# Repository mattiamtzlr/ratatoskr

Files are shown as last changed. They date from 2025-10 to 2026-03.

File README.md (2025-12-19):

# CS-358a Project: Ratatoskr (Micromouse)

Team members: Leoluca Bernardi, Leonardo Bolognese, Ali Gorgani, Mattia Metzler, Anthony Tamberg



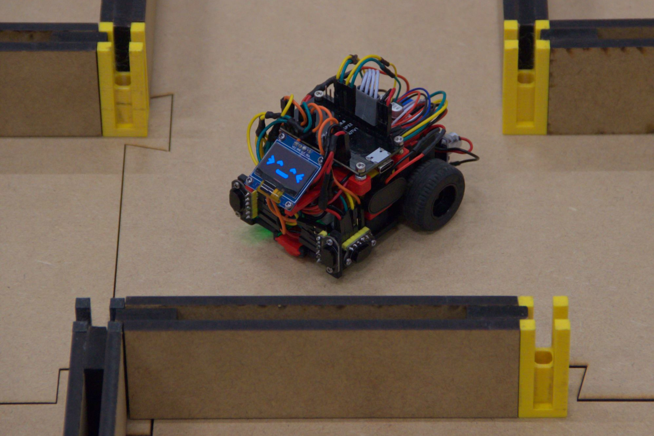
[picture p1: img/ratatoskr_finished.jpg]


## Table of Contents

<!-- mtoc-start -->

* [Introduction](#introduction)
  * [Inspiration and References](#inspiration-and-references)
* [Design](#design)
  * [Hardware](#hardware)
    * [Schematic](#schematic)
  * [Firmware and Software](#firmware-and-software)
    * [Firmware](#firmware)
    * [Software and Logic](#software-and-logic)
  * [The Maze](#the-maze)
* [Assembly](#assembly)
  * [3D-printing](#3d-printing)
  * [Soldering](#soldering)
  * [Chassis](#chassis)
  * [Drivetrain and Housing](#drivetrain-and-housing)
  * [Battery and ESP32 Mount](#battery-and-esp32-mount)
  * [OLED Mount](#oled-mount)
  * [Wiring, Motor driver and Power Supply](#wiring-motor-driver-and-power-supply)
    * [Communication Cable Trees](#communication-cable-trees)
    * [Battery Connector, Buck Converter and Motor Driver](#battery-connector-buck-converter-and-motor-driver)
    * [ESP32](#esp32)
    * [XSHUT Cables](#xshut-cables)
* [Software Setup](#software-setup)
  * [PIO Setup](#pio-setup)
  * [MMS Setup](#mms-setup)

<!-- mtoc-end -->

<br>

## Introduction

Ratatoskr is a small autonomous robotic 'micromouse' that can find the fastest path through a maze.
In two separate `search` and `run` phases, the mouse first finds the most optimal path and then traverses it, doing
both in the shortest possible time. In this project we designed a compact micromouse capable of traversing a maze
smoothly, precisely, and efficiently, allowing it to take diagonal paths during the final `run`.  
Below is a video showing both these phases. The start is marked in blue and the goal in red. The `run`
phase starts once the mouse has returned back to the start.

https://github.com/user-attachments/assets/a93646fe-425e-46f5-a616-213aecb9d267

### Inspiration and References

This project is inspired by the micromice of a previous iteration of the course, specifically
[MinosMouse](https://github.com/epfl-cs358/2024fa-minosmouse) and
[PicoMouse](https://github.com/epfl-cs358/2024fa-picomouse). We used their projects to get an idea of the needed
components and the general layout of the software.  
We also used parts of their maze for convenience and to save on resources and waste, because remaking these would
use a lot of material and time. There is more about this in the maze section.

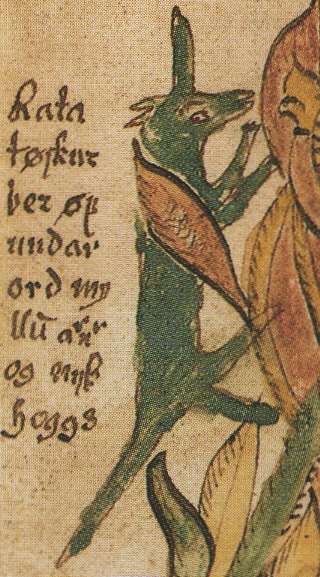
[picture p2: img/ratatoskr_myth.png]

Finally, the name 'Ratatoskr' comes from Norse mythology and refers to a squirrel that runs through the world-tree
Yggdrasil, carrying messages. We found this name to be quite fitting for our project, as Ratatoskr is one of the only
creatures capable of navigating the complex interior of Yggdrasil.
For your enjoyment, here is an image from a 17<sup>th</sup> icelandic manuscript depicting Ratatoskr, taken from Wikipedia
(public domain).

<br>

## Design

By design, most parts of Ratatoskr are fully 3D-printable, with the remaining parts being common Lego pieces.  
The final Micromouse weighs approximately 190g, it is 7cm wide and about 10cm long. About a quarter of the weight comes
from the 9V battery used to power it.

### Hardware

Ratatoskr requires the following electronic and mechanical components:
| Component | Quantity | Notes |
|---|---|---|
| N20 DC gear motor w/ encoder and connector | 2 | Working RPMs: 500, 750, 300[^1] |
| MX1508 motor driver | 1 | - |
| ESP32 development kit | 1 | **30-pin** version, higher should be fine |
| LM2596 buck converter | 1 | - |
| VL53L1X time-of-flight sensor | 4 | Also known as `TOF400C` |
| MPU-6050 3-axis accelerometer w/ gyroscope | 1 | - |
| SSD1306 OLED screen | 1 | These come in multiple colors, we used hybrid yellow-blue |
| 9V (PP3) battery w/ connector | 1 | We recommend using good quality batteries for this, as the current should be somewhat stable |
| LEGO(r) 58090 Tire 30.4 x 14 Solid | 2 | Other tires of approximately the same size should work |
| LEGO(r) 3705 Technic Axle 4L | 2 | - |

[^1]: Not tested, but should work given the torque and speed requirements

#### Schematic

Below is the full electronics schematic of ratatoskr.

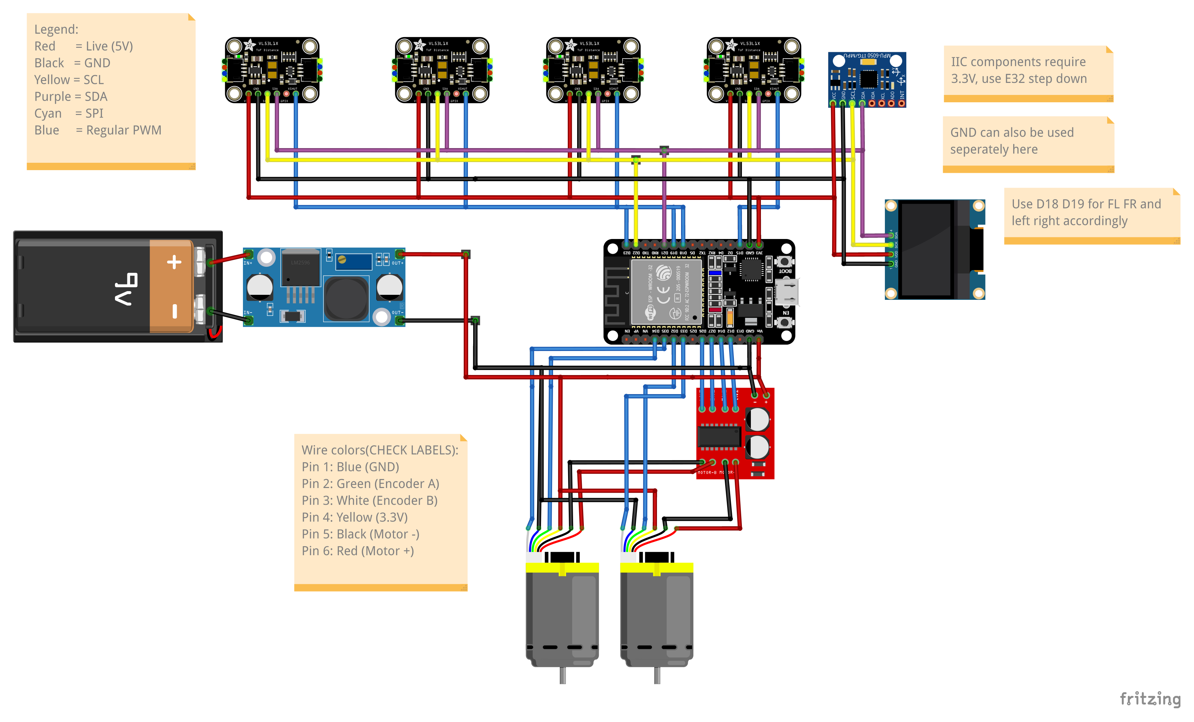
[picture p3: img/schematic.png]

Note that the exact pinout of the components might differ depending on the manufacturer and version of each part.

### Firmware and Software

Below follows a very brief overview of how the software for Ratatoskr works. For more details look at the source code :wink:

#### Firmware

We use the following libraries to simplify the hardware interfaces:

| Library | Used for |
| --- | --- |
| [pololu/VL53L1X](https://github.com/pololu/vl53l1x-arduino) | ToF sensors |
| [ronny-antoon/NVSDatabase](https://github.com/ronny-antoon/DatabaseAPI) | Flash storage database |
| [adafruit/Adafruit_SSD1306](https://github.com/adafruit/Adafruit_SSD1306) | OLED screen |
| [robjen/GFX_fonts](https://github.com/robjen/GFX_fonts) | Font for the OLED screen |

Additionally, we use [PlatformIO](https://platformio.org/) to compile the source code for the ESP32 and to handle all
the libraries above. See [PIO Setup](#pio-setup) for more details.

All sensors communicate with the ESP over the I<sup>2</sup>C protocol because the components can be assigned to
different addresses. As a result, we can use the same SDA and SCL pins for them. ToF sensors additionally require an extra pin for some XSHUT logic. The OLED is also controlled via I<sup>2</sup>C.  
There are C++ classes for most components that handle all their low-level functionality and provide a clean, high-level
interface for interacting with them.

#### Software and Logic

To make testing easier we use [MMS](https://github.com/mackorone/mms), a micromouse simulator. It allows us to test the
higher level code that handles solving a maze and calculating the final run without physically needing to run Ratatoskr
in a maze.

<p align="center"><video src='https://github.com/user-attachments/assets/aed72121-12ea-4d18-b9f5-ffeec3736798' height=100 width=100/></video></p>

Ratatoskr uses _principal-integral-derivative_ (PID) controllers to generate precise and stable movement. These
controllers continually adjust the motor power based on sensor feedback, allowing the micromouse to correct itself on the
fly. There are three PID systems in total:

1. Motor encoders: ensure that both wheels spin at the same, correct rate allowing for controlled acceleration.
2. Side ToF sensors: ensure the mouse stays centered between the walls and generally positions itself correctly in the
   maze.
3. Front ToF sensors: ensure that the mouse stays centered during diagonals and detect the end of diagonals.

To find the best path in the maze, Ratatoskr uses a floodfill algorithm while regularly updating its image of the maze
using the sensors. The best path is then computed from a Dijkstra graph constructed from this information. The Dijkstra
algorithm is tuned to favor diagonals over turns. This path is finally further optimized to combine multiple forward
movements into one so that Ratatoskr does not stop at every cell.

Documentation can be accessed by running `make docs` at project root. By using [Doxygen](https://www.doxygen.nl/index.html)
and a [CSS extension](https://github.com/jothepro/doxygen-awesome-css/tree/1f3620084ff75734ed192101acf40e9dff01d848) all
function headers get collected into a nice multipage format including function headers, descriptions, and call-graphs.

### The Maze

The maze we use for Ratatoskr uses the same wall pieces and mounting posts designed by the previous year's micromice teams, although with a newly
designed tiled floor. The posts are 3D-printed with a pocket for an M2.5 nut. The walls and baseplates are lasercut
from MDF.  
As a sidenote, it probably would have been better to redesign the posts and walls because they are not easy
to assemble and use. However, to save resources and time, we decided to go with the existing ones.  
To mount the posts to the baseplates, use M2.5 flathead screws, which can be countersunk to the underside of
the baseplates with a tapered (hand) drill. The walls are simply slid in between the posts.

The baseplates are designed to interlock like puzzle tiles, eliminating the need for complex mounting

Below is a technical drawing of a maze baseplate.

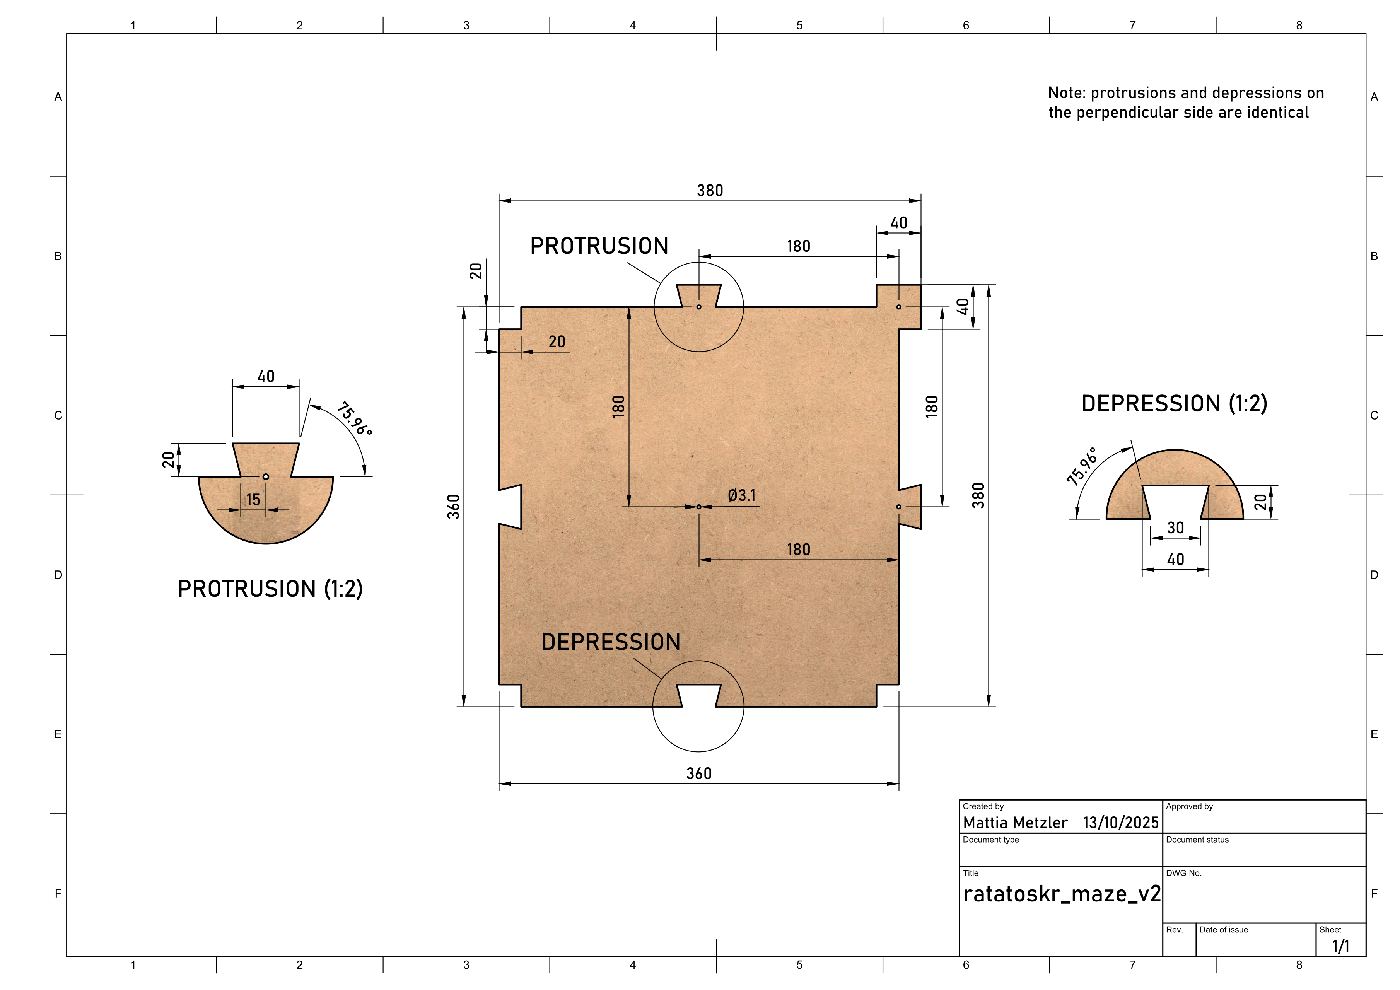
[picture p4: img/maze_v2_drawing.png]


<br>

## Assembly

To assemble Ratatoskr, the following additional hardware is needed:

| Item | Quantity | Note |
| --- | --- | --- |
| M2.5 threaded inserts | 6 | 4x for ESP32 mount, 2x for chassis |
| 2.5mm washers | 6 | Used to increase mount height of gyro |
| 5mm washers | 2 | Used to reduce friction between wheel and chassis |
| M2.5 nuts | 6 | 2x for gyro, 4x for ESP32 mount |
| M2.5 10mm machine screws | 8 | 2x for battery holder, 2x for gyro, 4x for ESP32 mount |
| M2.5 5mm machine screws  | 3 | 2x for buck converter, 1x for motor driver |
| M2 5mm machine screws | 12 | 2x for each ToF sensor, 4x for OLED |

In addition:

- Various jumper cables, depending on the amount of serviceability desired.
- There is an alternative version of the ball caster piece (see below) which has a screw hole for a M2.5 5mm machine
screw to reduce wear on the plastic. We found however that that version leads to more snagging on the maze tile borders.

### 3D-printing

The following STL files need to be 3D-printed:

| STL file | Quantity | Description and Notes |
| --- | --- | --- |
| `./CAD/STL/miter_gear.stl` | 4 | Drivetrain gears |
| `./CAD/STL/lego_adapter_v2b.stl`  | 2 | Motor shaft adapters, **brim recommended** |
| `./CAD/STL/screen_mount.stl` | 2 | OLED screen mounts, **brim needed** |
| `./CAD/STL/v2/ball_caster.stl` | 1 | Ball caster, **Supports recommended** |
| `./CAD/STL/v2/battery_clip.stl` | 1 | Battery clip |
| `./CAD/STL/v2/battery_holder.stl` | 1 | Battery holder, **Supports needed** |
| `./CAD/STL/v2/chassis_cutout.stl` | 1 | Latest, Lightest ver. of chassis, **supports needed for axle holes and sidewall cutouts** |
| `./CAD/STL/v2/middle_shelf.stl` | 1 | Shelf to mount gyro on |
| `./CAD/STL/v2/top_shelf.stl` | 1 | Shelf to mount motor driver on |

It is recommended to print all parts on Prusa MK4 printers, splitting the job into two prints: the chassis and the
remaining components.  
After that is done, heat-set the threaded inserts into the battery holder and the chassis:

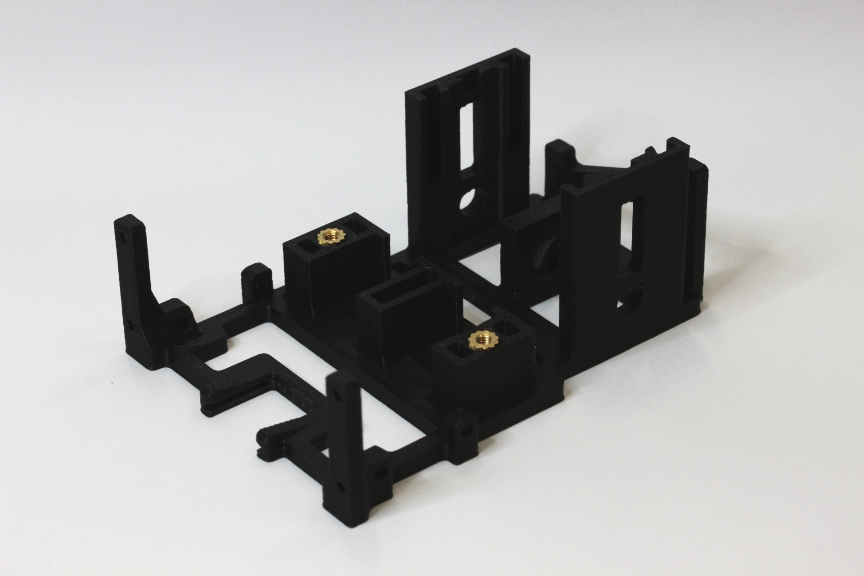
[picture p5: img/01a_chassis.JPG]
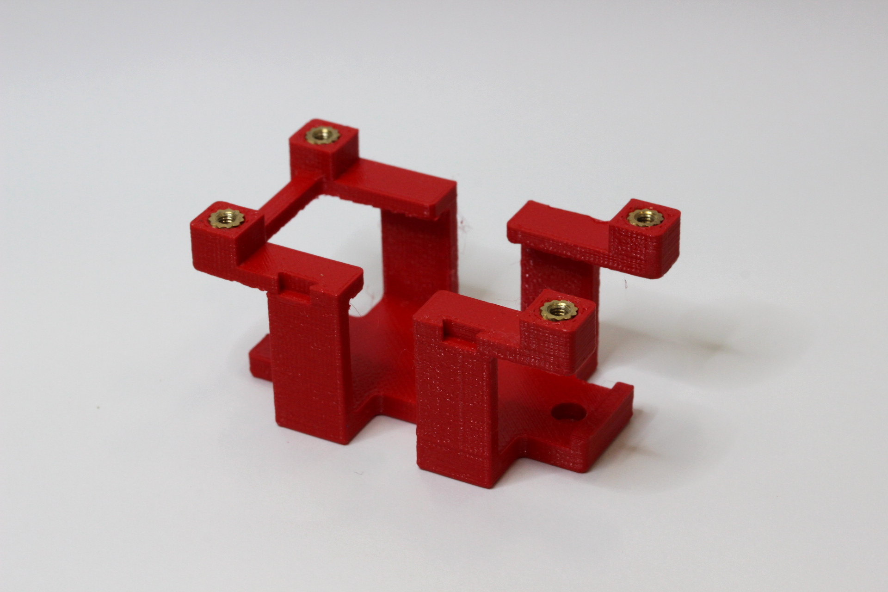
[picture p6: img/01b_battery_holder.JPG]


### Soldering

Solder the pin headers to the OLED, the ToF sensors and the gyroscope. Use the bent headers for the ToF and the gyro,
inserting them from below for the ToFs and from above for the gyro. Bending the OLED headers inwards slightly helps.  
For more details see photos further below.

### Chassis

Insert the inverted (!) ball-caster into the cutout in the front. You shouldn't need to sand this much once the supports
are removed, as it has been designed with the right tolerances.  
Mount the ToF sensors as shown below to the chassis using 2x M2 5mm screws each.

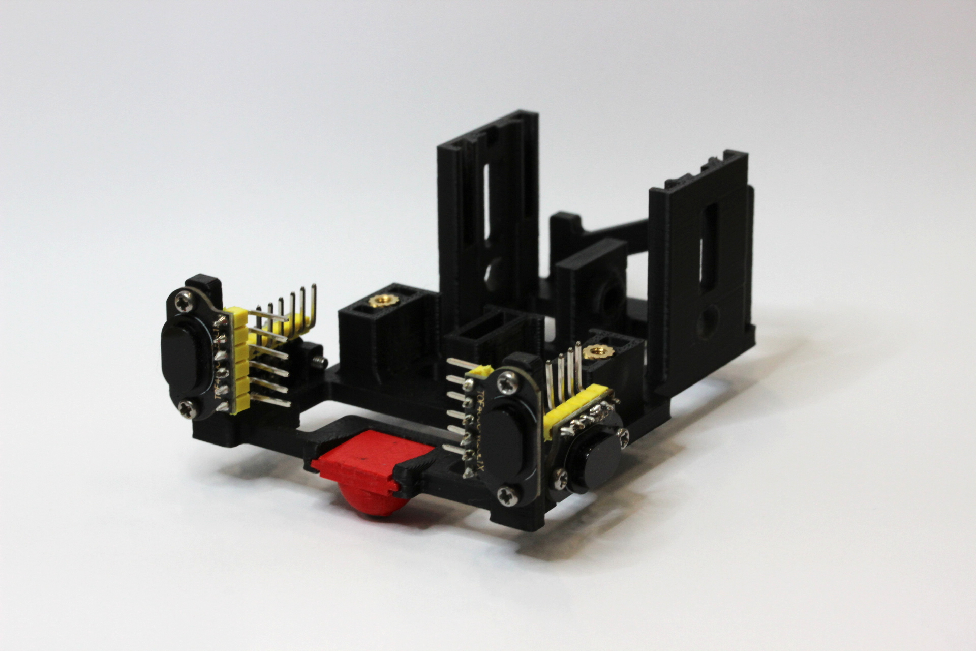
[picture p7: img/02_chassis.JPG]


### Drivetrain and Housing

Screw the gyro to the middle shelf of the drivetrain housing making sure to put three (3) washers between the underside
of the gyro and the shelf, and a nut at the underside of the shelf. Use 2x M2.5 10mm screws. Take note of the
orientation of the gyro in the picture below -- the back edge of the gyro should be aligned with the edge of the shelf.  
Then slide the shelf down the rails in the drivetrain housing. Again, you will probably need to sand/file some things here.

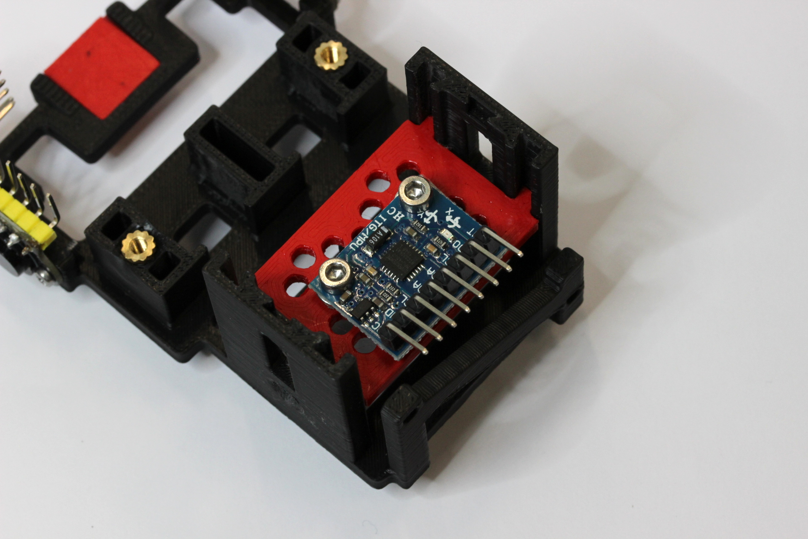
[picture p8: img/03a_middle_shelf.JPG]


Put one adapter over each motor shaft and slide on a gear. Insert the LEGO axles into the assembled wheels, put the
washer on top and slide them through the axle holes in the chassis, while simultaneously putting in the second set of
gears. This step is somewhat tricky but well doable with some pliers or tweezers.  
Before doing this, you need to file down the insides of the axle holes (including the holder in the middle) to make sure
the wheels turn freely. This is again somewhat finnicky but well doable with a small round file.

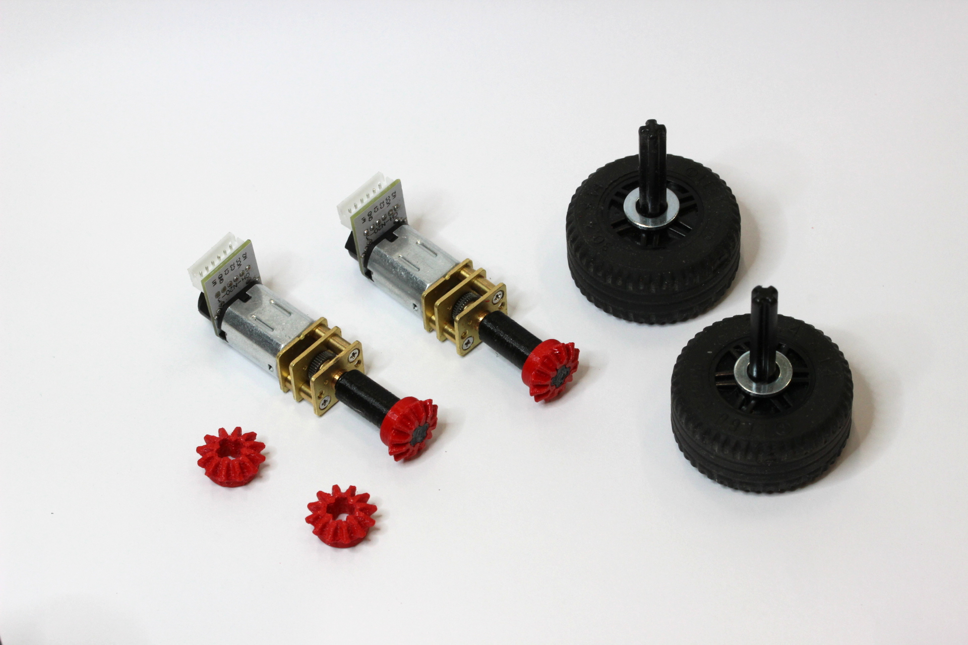
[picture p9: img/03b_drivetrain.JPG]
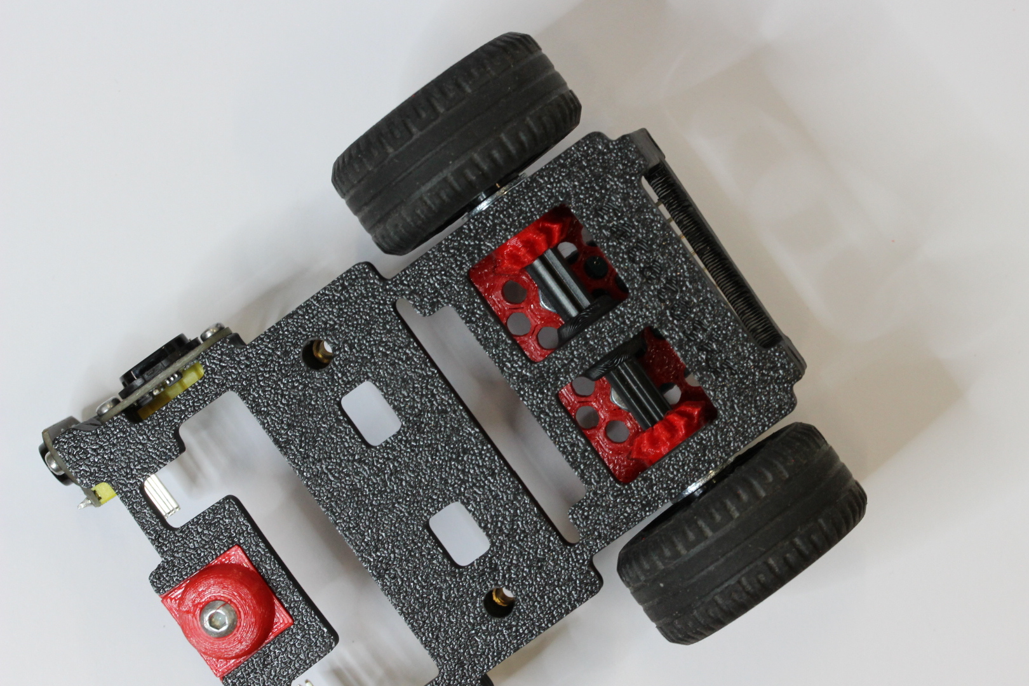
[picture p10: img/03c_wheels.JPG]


Finally, insert the motors as shown below. You might need to turn the wheels a bit so the gears mesh well.

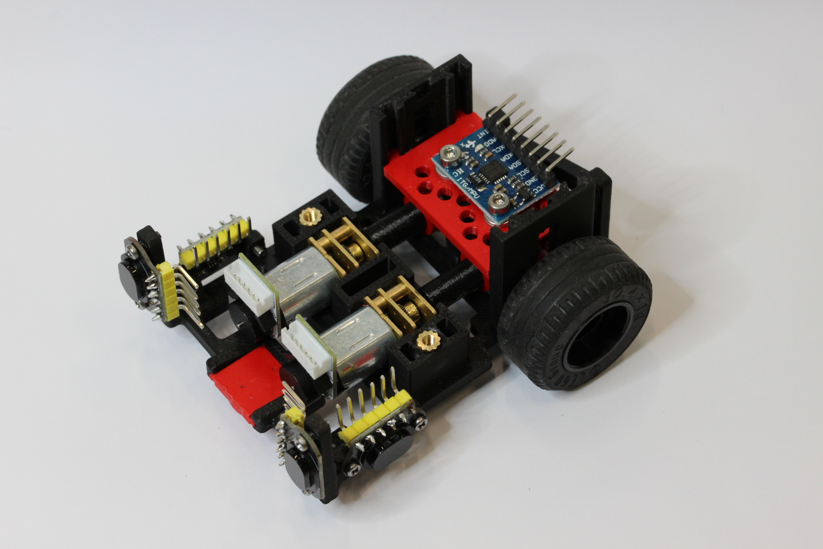
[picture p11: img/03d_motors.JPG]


### Battery and ESP32 Mount

Use 2x M2.5 10mm screws to screw the battery holder to the chassis using the previously installed threaded inserts. Make
sure to orient the battery holder correctly, the cutouts for the OLED mounts should be facing forwards. Alternatively,
check that the little connecting bar on one side of the battery holder faces the right-hand side.  
Also make sure that the screws are inserted all the way, i.e. the heads should sink into the cutouts made for them.

At this point you can slide in the battery and secure it from behind using the little clip.

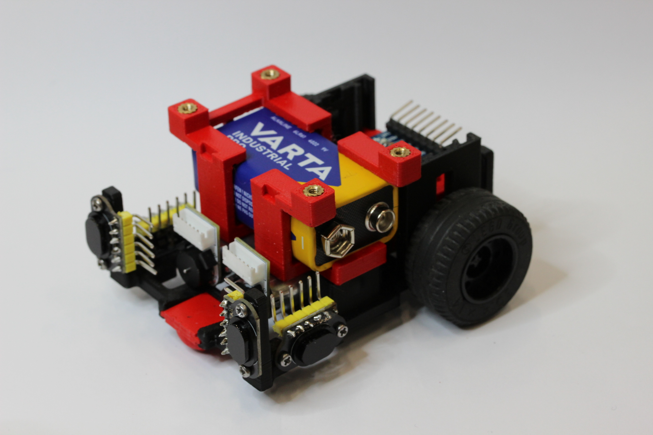
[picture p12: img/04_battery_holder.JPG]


### OLED Mount

Using 4x M2 5mm screws, screw the OLED mounts to the OLED board like in the below photo:

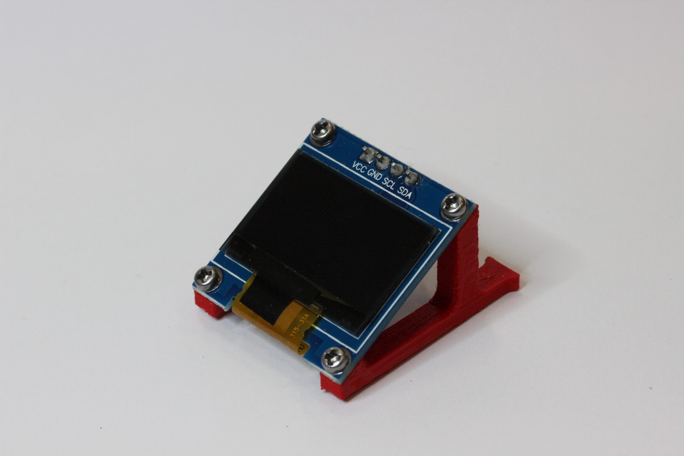
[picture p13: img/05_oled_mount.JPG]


### Wiring, Motor driver and Power Supply

Now for the hard part! :wink:

#### Communication Cable Trees

You need to wire **four** (4) cable trees with female dupont connectors for the
I<sup>2</sup>C communication as follows:

- four (4) connectors for the ToF sensors
- one (1) connector each for the gyro and the OLED

Therefore you need (6) female connectors in total, first split into two, one for ToFs/OLED and one for gyro, the former
then further split into five.  
We recommend keeping the colors between the trees different so they are easier to tell apart, as in the photos below.

> [!WARNING]
> It is crucial to make these cables the right length. Too short and you won't be able to connect the components, too long
> and there will not be enough space in the mouse to put all the cables. Measure the cables before you cut them by
> dry-fitting them on the mouse.

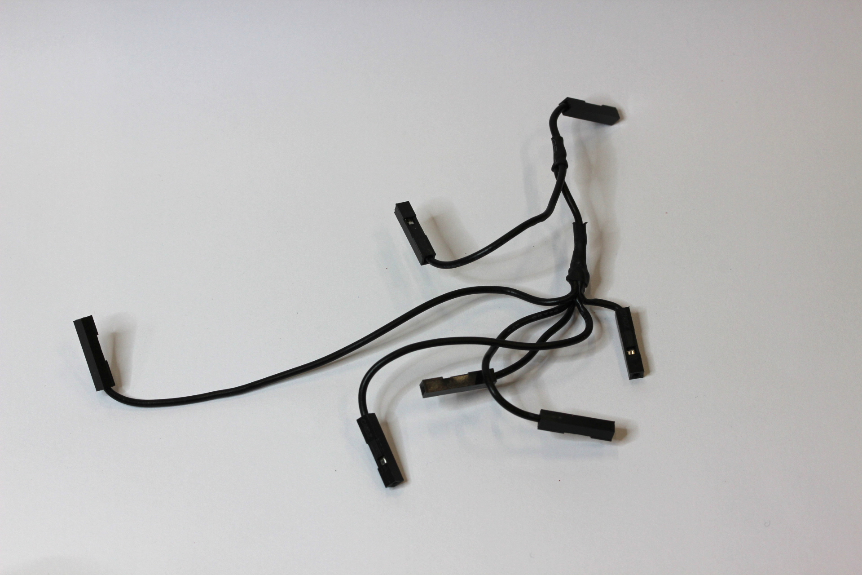
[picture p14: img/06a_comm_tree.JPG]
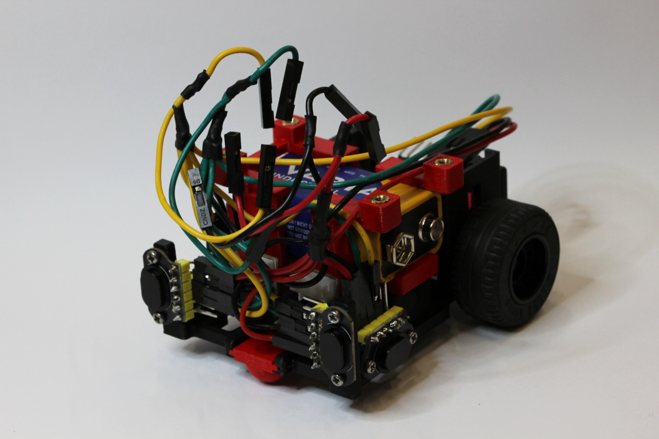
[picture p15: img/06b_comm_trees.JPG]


The four down-facing unused connectors in the above picture are used for the OLED screen, which can also be mounted now
by sliding it into the cutouts on the battery holder.

#### Battery Connector, Buck Converter and Motor Driver

The buck converters `IN +` and `IN -` pads need to be soldered to the power (red) and ground (black) cables of the
battery connector respectively. Then, with a multimeter connected to the `OUT +` and `OUT -` pads, the brass screw on
the buck converter needs to be turned (probably counter-clockwise) until the voltage read is around 5V. The LED on the
buck converter should light up quite strongly when the battery is connected.

Then wire up **two** (2) cable trees for 5V and GND going from one cable to four each. As the power wires need to be
reliable, these should be soldered directly, not using Dupont connectors. Thus only add Dupont connectors to one of the
four cables, namely the one for the ESP32.  
Then wire the other three cables to the motor drivers and the motors directly. Finish soldering the motor driver as shown
on the [schematic](#schematic).  
The encoder and motor input cables should also end in Dupont connectors to connect to the ESP32.

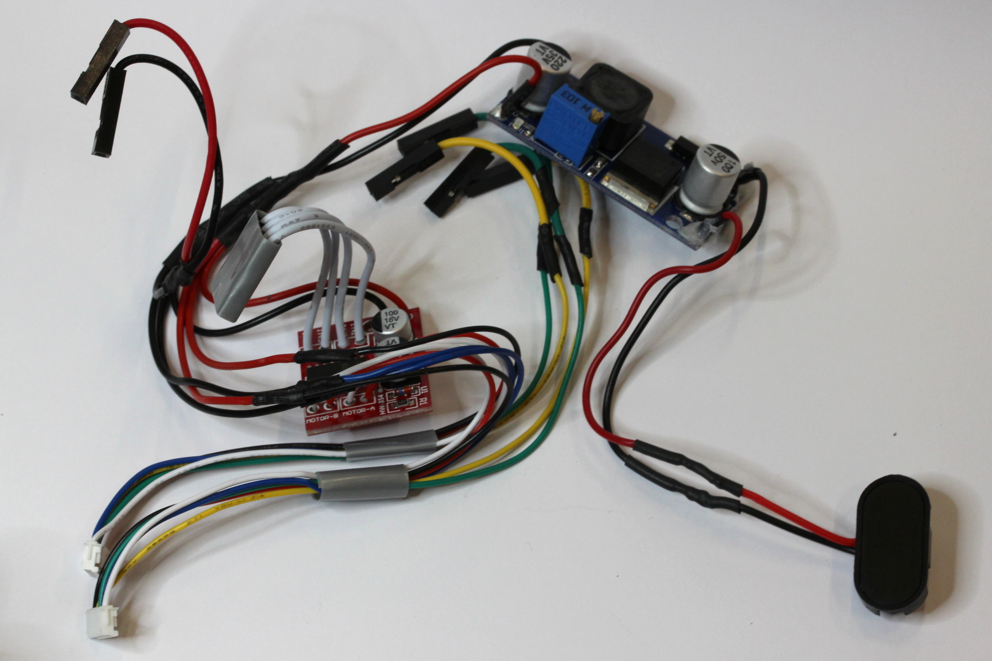
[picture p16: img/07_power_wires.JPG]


Finally, mount all of this to the mouse, making sure that the motors are plugged in correctly. To do so, first mount
the motor driver to the top shelf using 1x M2.5 5mm screw. The buck converter is attached using the 2x M2.5 5mm screws.

#### ESP32

Now you can finally connect the ESP32 by screwing it **upside-down** into the threaded inserts. Then connect all
previous cables as specified on the schematic.

#### XSHUT Cables

The last step is to solder some short cables for the XSHUT pins on the ToF sensors. These should be just long enough to
connect, but not be too long as they might not have enough space otherwise.

And you are done! Enjoy your finished micromouse! :smile:

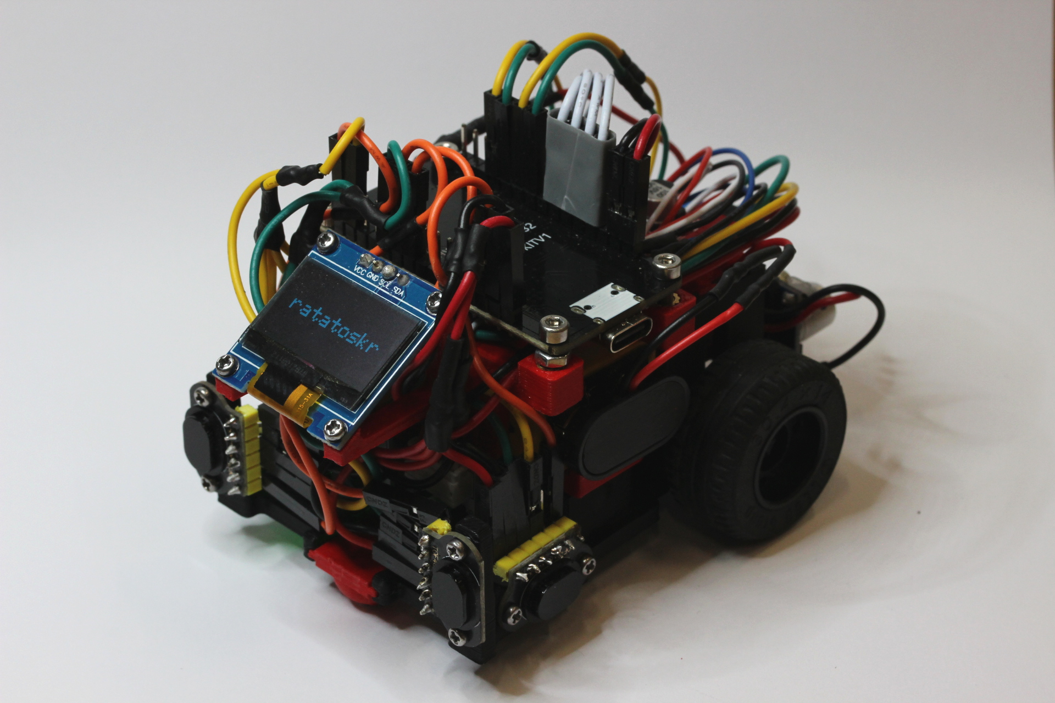
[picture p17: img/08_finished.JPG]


## Software Setup

### PIO Setup

The [`platformio.ini`](./platformio.ini) file specifies the environment of the project, telling PlatformIO the
microcontroller and the libraries needed for compilation and flashing. The easiest way of interacting with PlatformIO is their
[CLI](https://docs.platformio.org/en/latest/core/index.html) which is used as follows:

- Compile the project
    ```sh
    pio run
    ```
- Upload the project to the ESP32
    ```sh
    pio run --target upload
    ```
- Open the serial monitor
    ```sh
    pio device monitor
    ```

All of these commands need to be run from the root directory of this repository.

> [!WARNING]
> Before doing anything for the first time, run
>
> ```sh
> pio run --target compiledb
> ```
>
> from the command-line in the root directory to generate `compile_commands.json` which tells `gcc/clang` how to compile
> everything.

### MMS Setup

To set up MMS, you first need to download the version of MMS corresponding to your operating system on the [MMS releases page](https://github.com/mackorone/mms/releases).



At the top right of your MMS window, you will find a box titled _Config_.

- Press the `+` button to create a new configuration.
    - Choose any _Name_
    - Choose the project root directory for the _Directory_ field
    - Enter `make sim` as _Build Command_
    - Enter `./out/sim.out` as _Run Command_
    - Click ok
- The button with the color wheel is a simple way to adjust the colors of the simulation.



Now you are ready to run the simulation.

- Press the `Build` button to compile the mouse code.
- Press the `Run` button to make it start.
    - Moving the scale from :turtle: to :rabbit: will increase the speed.

> [!WARNING]
> If you are using windows, a unix dependency may cause an error.
>
> To fix this, change line 6 of `virtual_mouse.cpp` from `#include <unistd.h>` to `#include <windows.h>`

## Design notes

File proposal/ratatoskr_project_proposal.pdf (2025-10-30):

Ratatoskr | CS-358a

## Ratatoskr

Leoluca Bernardi, Leonardo Bolognese, Ali Gorgani, Mattia Metzler, Anthony Tamberg

## Contents

## 1. Abstract

Ratatoskr is a small autonomous wheeled robot, a ‘micromouse’, that can find the fastest path through a maze. In two separate search and run phases, the mouse finds the most optimal path and then traverses it, accomplishing both in the shortest possible time. This project’s aim is to improve the design and software of the previous year’s micromice, as well as the design of the maze that they solve. The final result will be a faster micromouse wandering a smoother maze.

## 2. The Maze

Our maze for Ratatoskr will be made up of cells measuring 18 cm per side. Previous designs used modular walls made from 16cm planks attached to posts, but the posts were held in place with Velcro instead of screws. This caused misalignment and uneven walls, which negatively affected the performance of the micromouse.

Our new design (see Figure 1) reuses the wall pieces from last year, but using their intended screw-in attachment. Each floor tile covers a 36×36 cm²
area, not including the connecting attachments. One such tile fits four maze cells. The posts will be screwed directly into the tiles, keeping the structure rigid and aligned. The thickness of the tiles will be between 3-5 mm and with countersunk screw holes, these tiles will sit flush on the ground.

The tiles have been designed so that seams in the floor only run perpendicular to any path taken through the maze, so that the wheels of the micromouse cannot be caught in between two tiles.

### 2.1. Technical Drawing

Below is a technical drawing of the tile, showing it’s exact dimensions in millimeters.

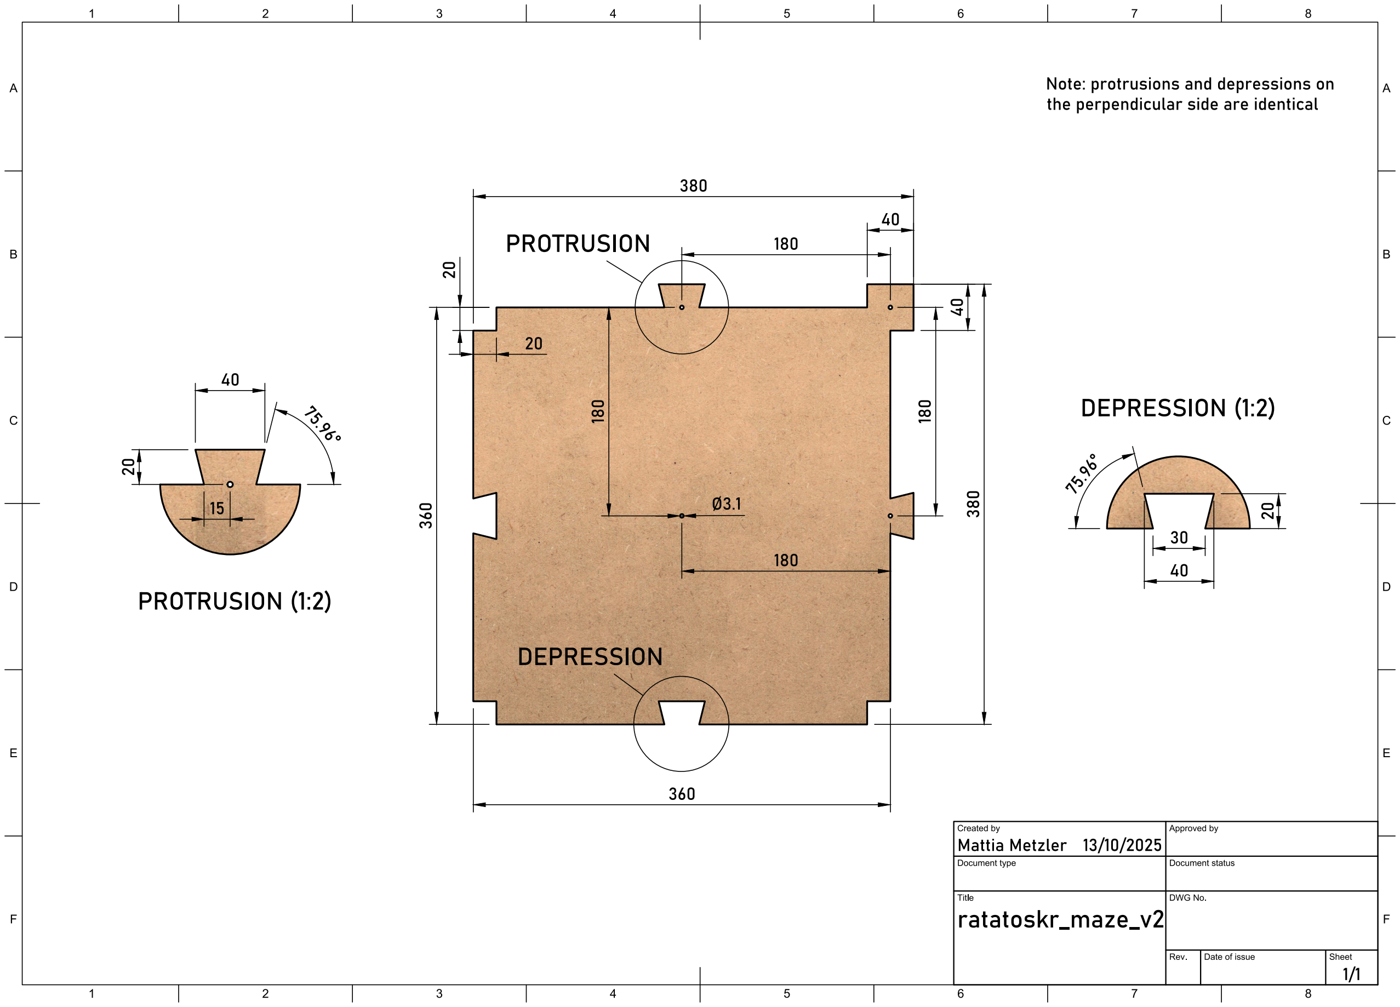
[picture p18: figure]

Figure 1: Technical drawing of the maze floor tile (created using Autodesk Fusion360)

## 3. The Mouse

This project builds upon last year’s MinosMouse design, incorporating ideas from the Picomouse project and introducing several of our own improvements. Namely, one improvement is the ability to traverse diagonals in a completely straight line, as opposed to a zigzag motion. To accomplish this, we’ve decided on a combinations of motor encoders, sensors, and a gyroscope to accurately track the position and orientation of the mouse.

The Competition
Even though Ratatoskr will probably not compete in official MicroMouse competitions, we will still adhere to their rules, which are linked in full in Section 8.
We will also measure Ratatoskr’s performance according to the official rules, which state:
1. Each mouse is allowed a maximum of 10 minutes to perform.
2. The scoring of a micro mouse shall be obtained by computing a handicapped time for each run as follows:

ttotal = trun +

1
30

⋅ tsearch + ptouch

where ptouch is a touch penalty and is calculated as ptouch = 3 +

1/10⋅ trun. It is only added if the mouse has been touched at any time between the search and the run.

These rules ensure that mice which use a lot of their maximal time finding the optimal path are penalized accordingly, as the goal of a good micromouse is to be not only fast but also efficient.

### 3.1. Design and Technical Drawing

Below is a technical drawing of the mouse, showing the design from multiple angles as well as some of its dimensions in millimeters. Note that these drawings don’t yet include the newly conceptualized sensor layout as described in Section 3.2.3.

Figure 2: Technical drawing of Ratatoskr (created using Autedesk Fusion360)

### 3.2. Hardware

We will walk through the list of major hardware components used in Ratatoskr, explaining the reasoning and purpose of our choices.

### 3.2.1. Motors, Drivers & Encoders

Just like previous proven attempts, Ratatoskr will use two N20 DC gear motors with 750 RPM and built-in Hall encoders. We decided to keep this motor type since they’ve proven reliable and compact. The encoders allow for accurate position and speed control, which is necessary for both precise maze exploration and fast traversal.

The motors will be driven by an Adafruit DRV8871 DC Motor Driver Breakout Board (3.6 A max). We chose this driver since it offers a higher current limit and overall better efficiency, while remaining compact and easy to interface with. The DRV8871 provides reliable bidirectional control through standard PWM and direction pins, which makes it perfectly suited for our differential drive setup.

The ESP32 will generate PWM signals for each motor and handle encoder interrupts to read wheel rotation. This setup allows us to precisely regulate motor speed and direction while keeping the driver circuit simple and robust. The driver also includes built-in protection features such as current limiting, thermal shutdown, and undervoltage lockout, reducing the risk of hardware failure during testing.

We plan on using the encoders to estimate distance and direction by comparing the ticks of both wheels. This gives us an internal odometry system that can be cross-checked with the gyroscope and wall sensors later on.

For power, the motors run directly off the 7.4V LiPo battery¹
through the driver, while the rest of the system will be powered through a buck converter that brings the voltage down to 5V for logic and sensors. The encoders connect to interrupt-capable GPIO pins on the ESP32.

Overall, the hardware control of the motors will stay very similar to previous years’ designs, but we will focus more on improving wheel control through better PID tuning and the combined use of encoder and gyro data to reduce slippage and drift. More importantly, we will aim to develop a combination of hardware and software for Ratatoskr to be able to traverse diagonals within the maze structure efficiently.

### 3.2.2. Gyroscope

For measuring orientation and rotational velocity, we are using an MPU-6050 IMU module. It’s a 6-axis sensor that provides both accelerometer and gyroscope data over I²C, and is commonly used in small robotic systems like ours.

The main purpose of the gyroscope is to keep track of Ratatoskr’s direction and correct drift that occurs from wheel slip or uneven surfaces. During runs, the gyroscope will be used to ensure straight motion (keeping angular velocity close to zero) and to control turns precisely by integrating angular velocity until the desired rotation angle is reached.
The IMU connects via I²C to the ESP32, and readings will be used with the wheel encoder data to improve reliability. At startup, the gyroscope will calibrate itself by measuring bias when the mouse is stationary. This zeroing process is necessary to prevent drift during longer runs.

We considered switching to a higher-end IMU (like the BMI160 used in some previous projects), but decided that the MPU-6050 is sufficient and easier to source locally. If we later notice

1Although initially, we will be using dry cell batteries for power high drift or inconsistent readings, the module can be replaced without any major hardware or software changes, since the communication protocol remains the same.

### 3.2.3. TOF sensors

For wall detection and distance measurement, we are using four Time-of-Flight (ToF) sensors, similar to the setup used previously but slightly adjusted for our own needs. The sensors will help Ratatoskr detect nearby walls and align itself accurately within the maze.

We will use two VL53L4CD sensors facing forward to detect walls ahead of the mouse and to measure break distance at high speed. These long-range sensors allow the mouse to slow down early before hitting a wall and to plan turns smoothly.
Additionally, we will use two VL6180X sensors placed on the left and right sides of the mouse. These are short-range sensors used for centering between walls and for detecting open paths or intersections. The combination of both types gives us accurate coverage around the front half of the mouse.

All four sensors communicate over I²C. Since they share the same default address, each one will be assigned a unique address during initialization using the XSHUT pins, or controlled through the I²C multiplexer (see Section 7.)

In operation, the forward sensors will be used mainly for detecting walls and deceleration, while the side sensors will continuously poll and measure distances to maintain alignment. The software will filter these readings to ignore invalid values and handle possible occasional reflections from the maze which may mess with the sensors. This arrangement gives Ratatoskr a good field of view while avoiding the sensors overlapping and interfering with one another. See also Figure 4 for an overview of how these sensors will be used to navigate turns.

### 3.3. Software

The software for this project will be loosely based on the previous iterations that we have access to and therefore use C++ as it was used in both projects and is generally the language of choice for such applications. We have decided on using the Google formatting style but using 4 spaces of indent, enforceable using the .clang-format file. All code that is not directly interacting with hardware should be testable without access to the mouse using unit tests and the mms (https://github.com/mackorone/mms) micromouse simulation software.

### 3.3.1. Hardware Interfaces

We will need some software interfaces to communicate with the hardware mentioned earlier, the details of which are listed in the following.

### 3.3.1.1. Motor Interface Overview

The Adafruit DRV8871 (https://cdn-learn.adafruit.com/downloads/pdf/adafruit-drv8871-brushed-dc-motor-driver-breakout.pdf) DC Motor Driver Breakout Board provides two input pins (IN1 and IN2) that control the H-bridge and can accept PWM signals up to ~200kHz. The board supports 6.5–45V motor supply and up to 3.6A peak current, with built-in protections for overcurrent, thermal shutdown, and undervoltage lockout.

Attributes

in1_pin | first input pin connected to ESP32 PWM/logic GPIO
in2_pin | second input pin connected to ESP32 PWM/logic GPIO
pwm_channel | ESP32 PWM channel (if hardware PWM is used)
max_pwm | upper limit for PWM duty (0–255 or 0–1023 depending on mode)
target_duty | last commanded PWM duty cycle
direction | current direction (“forward”, “backward”, “brake”, “coast”)

Methods

init() | sets up both pins as outputs, attaches PWM channel, and ensures driver is idle.
set_speed(duty) | writes PWM value to selected input and LOW to the other pin.
forward(speed) | sets IN1 = LOW, PWM on IN2.
backward(speed) | sets IN2 = LOW, PWM on IN1.
brake() | drives both pins HIGH (active braking).
coast() | drives both pins LOW (free spin).
stop() | alias for coast(), used when idling or shutting down.
test_ramp() | optional helper to sweep PWM up/down for diagnostics.

Example usage

motorL = MotorDRV8871(in1_pin=25, in2_pin=26) motorL.init()

# run forward half speed

motorL.forward(128)

# brake briefly, then reverse motorL.brake()

delay(0.2)
motorL.backward(200)

motorL.stop()

All motor instances share the same pattern: one DRV8871 per wheel, each controlled through two GPIOs. Speed control is achieved purely through PWM duty cycle, and the higher-level motion control (PID, odometry, etc.) determines the duty target.

To conclude:

(IN1 = LOW) ∧ (IN2 = PWM) → Forward (IN1 = PWM) ∧ (IN2 = LOW) → Backward (IN1 = LOW) ∧ (IN2 = LOW) → Coast (IN1 = HIGH) ∧ (IN2 = HIGH) → Break

This layout gives us a clean, hardware-agnostic motor interface that remains valid even if the driver is swapped later (as long as it accepts PWM + DIR logic inputs).

### 3.3.1.2. ToF Interface Overview

Both ToF sensors speak I²C and measure distance via laser time-of-flight. The short-range VL6180X (https://cdn-learn.adafruit.com/downloads/pdf/adafruit-vl6180x-time-of-flight-micro-lidar-distance-sensor-breakout.pdf) reliably covers up to ~200 mm which is ideal for side-wall centering, while the longer-range VL53L4CD (https://cdn-learn.adafruit.com/downloads/pdf/adafruit-vl53l4cd-time-of-flight-distance-sensor.pdf) covers up to ~1.2 m allowing forward look-ahead for fast runs. We will provide one abstract interface class in software that handles initialization, reading distance, error checking and supports multiple sensors. Sensors will be configured individually (side vs front) but use the same underlying driver logic. This gives us a clean way to plug whichever breakout we use (or future upgrade) and ensures the maze-solving logic can simply ask “what’s my distance to wall X?” without worrying about the specifics.

All sensors share the same basic interface so they can be handled the same way, regardless of model or where they’re mounted (front or side).

Attributes

addr | I

2C address (unique per sensor after initialization)
xshut_pin | GPIO pin used to enable or disable the sensor
role | “front” or “side” (determines config like range and polling rate, can be enum)
distance | last valid distance reading (in mm)

valid | flag showing if the current reading is valid
timestamp | last time a valid reading was taken

Methods

init() | powers up the sensor, assigns I²C address, sets measurement mode and timing.
start() | begins continuous measurements or enables periodic polling.
read() | reads the latest distance value (returns distance in mm and a validity flag).
stop() | stops ranging and powers down the sensor (used when idling or resetting).
reset() | performs a soft reset if a sensor becomes unresponsive.
is_valid() | returns whether the current measurement is valid or timed out.
filter() | optional smoothing (median or moving average) to remove spurious spikes.

Example usage

tof_left = ToF(addr=0x2A, xshut_pin=17, role="side") tof_left.init()
tof_left.start()

distance, valid = tof_left.read() if valid:
print("Left wall:", distance, "mm") else:
print("No valid reading")
tof_left.stop()

All ToF sensors will be managed through a shared driver that loops over each sensor object, polling and updating readings in the background. This lets higher-level modules (e.g., centering or wall detection) just call something like get_wall_distance("left") without worrying about the hardware details.

### 3.3.1.3. Gyroscope Interface Overview

The MPU-6050 (https://cdn-learn.adafruit.com/downloads/pdf/mpu6050-6-dof-accelerometer-and-gyro.pdf) sits on I²C (default addr 0x68; 0x69 if AD0 is high) and provides 3-axis gyro + 3-axis accel. We only require readings from this module so we will aim for the interface to be very simple.

Attributes

addr | I 2C address (0x68 or 0x69)
gyro | latest gyro readings (x, y, z)
accel | latest accel readings (x, y, z)
timestamp | last time the sensor was updated
valid | flag indicating whether the last read was successful

Methods

init() | initializes I²C communication and wakes up the sensor.
start() | begins regular data polling from the IMU.
read() | returns the latest gyro and accel readings.
stop() | stops polling when the mouse is idle or powered down.
is_valid() | checks if the most recent data is valid.

Example Usage

imu = IMU_MPU6050(addr=0x68) imu.init()
imu.start()

gyro, accel = imu.read()
if imu.is_valid():
print("Gyro:", gyro, "Accel:", accel)
imu.stop()

This basic interface is enough for our needs: it lets us continuously read motion data and feed it into Ratatoskr’s movement and orientation logic.

### 3.3.2. Movement Control

We will use a class to streamline the control of the mouse and to create an API which is able to interact with the simulator.

- int mazeWidth()
- int mazeHeight()
- bool wallFront()
- bool wallRight()
- bool wallLeft()
- void moveForward(int distance = 1)
- void turnRight()
- void turnLeft()
- void setWall(int x, int y, char direction)
- void clearWall(int x, int y, char direction)
- void setColor(int x, int y, char color)
- void clearColor(int x, int y)
- void clearAllColor()
- void setText(int x, int y, String text)
- void clearText(int x, int y)
- void clearAllText()
- bool wasReset()
- void ackReset()

### 3.3.3. PID Controllers (Proportional–integral–derivative)

To make Ratatoskr’s movement precise and stable, we rely on PID control loops that constantly adjust the motor power based on sensor feedback. The idea is to let the mouse correct itself continuously on the fly.

In our implementation, we combine two kinds of control: one that regulates the wheel speeds through encoder feedback, and another that keeps the overall direction stable using the gyroscope. In practice, this means the encoders ensure both wheels spin at the correct rate, while the gyro makes sure the mouse maintains or changes its orientation exactly as commanded. Together they help Ratatoskr drive straight, turn cleanly, and recover quickly if one wheel slips.

The wheel speed PID adjusts the PWM sent to each motor so that the measured encoder speed matches the target speed. This keeps both wheels synchronized and allows for smooth acceleration. The PID in charge of direction, on the other hand, uses gyro and encoder data to correct deviations from the intended orientation. For instance, if the mouse starts veering slightly left or right while moving straight.

We will start with the PID parameters from MinosMouse as a reference, since they were tuned for a similar motor and weight setup. However, we’ll re-tune them for Ratatoskr’s specific mass distribution and the wooden maze surface. Tuning will be done empirically: testing response times, overshoot, and steady-state errors until the mouse can accurately complete physical test routes we will set up.

Each control loop runs at a fixed update rate (likely 500–1000 Hz), which is fast enough for stable control but not too heavy for the ESP32. The final PID equations will be implemented using integer arithmetic where possible to minimize floating-point overhead.

In short, the PID controllers ensure that Ratatoskr moves in a controlled, predictable way not too fast to slip, and not too slow to waste time. They also ensure that Ratatoskr will not crash into walls at very high speeds due to the fact that PID uses real-time data and automatically adjusts the movement. Once properly tuned, they’ll form the backbone of the motion control system.

### 3.3.4. Maze Solver

The mouse initially has no information on the maze which motivates the search traversal of the maze to discover the layout. As this phase is also timed and a fraction of it added to the final time, speed is not irrelevant. To save time we will employ an algorithm that increases the likelihood that the best path is inside of the explored labyrinth while not discovering every cell. The mouse needs to keep track of the walls present in each cell in order to construct a partial replica of the maze in its memory. We will approach exploration with a bias of moving towards the goal, where upon arriving the robot must make its way back to the start in order to initial the run phase. The way back to the start is used to discover more of the maze, once again using the floodfill algorithm. Using the micromouse simulator we can ensure that what the mouse wants to do is what it should do and optimize the path taken.

### 3.3.4.1. Diagonals

An additional issue for the solver will be the detection of diagonals. It should be possible to implement the detection of the type of diagonal and the encoding as post-processing steps that are applied to the path found by the simple solver. If time and resources allow, there is the possibility of refactoring the solver once the basic diagonals and straights work to search for the fastest instead of the shortest path. Further, the PID will need adjustments for the added complexity of sensor readings while traversing a diagonal.

### 3.3.5. LED Matrix & SD Card

As the battery on the micromouse is only sufficient for about half an hour of use, as observed by the MinosMouse team, we must make sure to waste as little battery life as possible. Thus, for debugging and logging we opt for a combined solution of an LED matrix and an SD card. This allows us to not be dependent on power-hungry systems like WiFi or Bluetooth.

The LED matrix will primarily be used during the runs, providing immediate feedback of the sensor data, for example which ToF sensors currently report a wall. A mockup of what this could look like can be seen in Figure 3.
The rest of the LEDs could be used to indicate other useful information, such as states of the state machine and so on.

The SD card will mainly be used after a run. It will collect and store information about the run at a much more granular level than the LED matrix could provide. Thus in combination, if a run has weird behavior, we can immediately check the LED matrix and then look at the debug data afterward.

The hardware-software interfaces for the LED matrix and SD card are quite simple, as they both use I²C for communication and there are well documented libraries for both, namely the Adafruit LED Backpack Library and the builtin SD library.

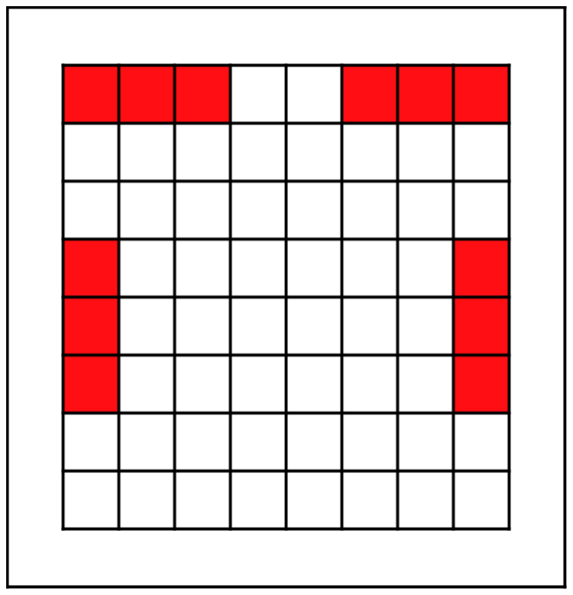
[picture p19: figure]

Figure 3: The LED matrix showing that all four sensors are currently sensing a wall

## 4. Tasks and Milestones

We have created a GANTT chart to provide an overview of the tasks to be done as well as their relations to the milestones and to each other.

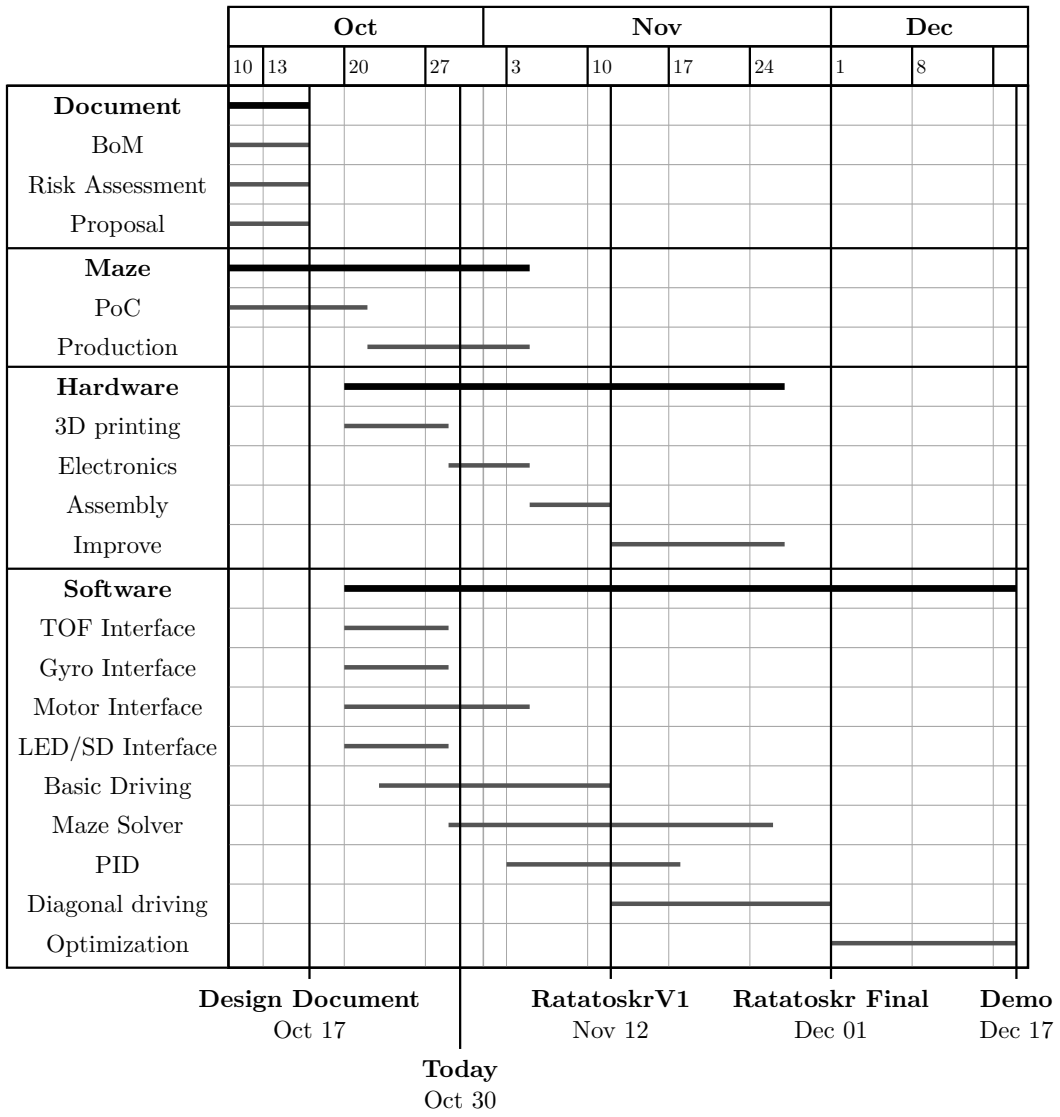
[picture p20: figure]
Document; BoM; Risk Assessment; Proposal; Maze; PoC; Production; Hardware; 3D printing; Electronics; Assembly; Improve; Software; TOF Interface; Gyro Interface; Motor Interface; LED/SD Interface; Basic Driving; Maze Solver; PID; Diagonal driving; Optimization; Oct; Nov; Dec; Design Document Oct 17; RatatoskrV1 Nov 12; Ratatoskr Final Dec 01; Demo Dec 17; Today Oct 30

### 4.1. Ratatoskr V1.0

The first version of the micromouse must be able to successfully maneuver and solve the maze in however much time it takes. This requires correct assembly and wiring of the physical components, working drivers for motors, gyroscope and sensors, a PID and an algorithm that can explore and solve the maze. At this points there is no need to worry about fancy turns or diagonals, a simple stop - turn 90° - go movement pattern will suffice, see type 0 in Figure 4.

### 4.2. Ratatoskr V1.1

To reach this milestone it is necessary to improve upon the first version by compressing successive forward movements into a single long straight. Further, the mouse should now be able to complete both type 1 and type 2 turns (Figure 4).

### 4.3. Ratatoskr V1.2

The next step will be to tackle diagonals. Requiring adjustments in the PID, two (possibly five) new turn types in order to efficiently and precisely handle entering, traversal and exiting. The algorithm composing the path for the final run will have to be adjusted to recognize diagonals and give the correct instructions.

### 4.4. Ratatoskr Final

The final version of our micromouse should be able to solve the maze by exploring it and then compute and execute a final run in which it never comes to a full stop, accelerates on long straights and speeds along diagonals where applicable.

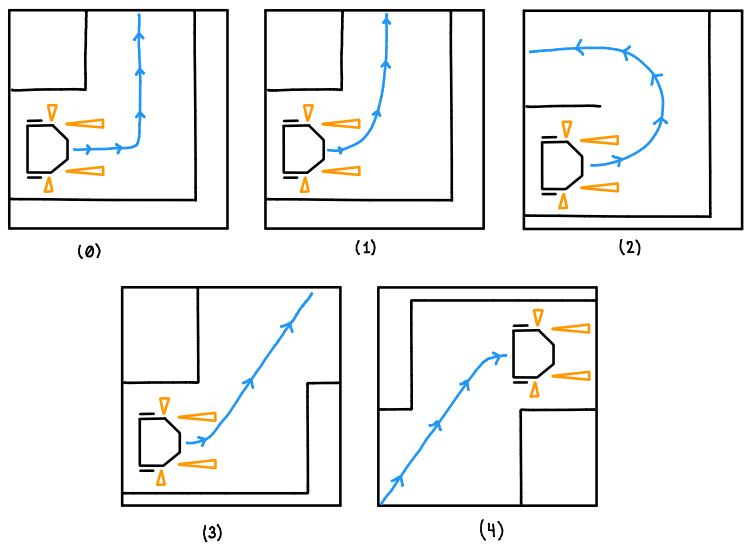
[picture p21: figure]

Figure 4: Turn Types

## 5. User Stories

As a member of the team working on Ratatoskr, I want the micromouse to be easy to service during development, for example by providing debug data after a run. Further, I want the finished micromouse and maze to be easy and moderately quick to set up and store, because I may want to show it off to friends.

More generally, as a person interested in making things I want to see that it is possible to create something fun and interesting, even with a limited background/knowledge in electronics and embedded programming.

As the professor I’d like parts of the project (or the project as a whole) to be reusable for future group or individual projects. Thus, I want the code and the design to be well-documented and modularized.

As a viewer of a micromouse competition I want the micromouse to perform well and be well-designed and compact. Optionally, it would be nice if the micromouse looked good, for example by incorporating some cosmetic aspects such as the LED matrix.

## 6. Risk Assessment

Regarding Ratatoskr, we will discuss the 3 elementary sources of issues and the risks they convey, namely hardware, software, and human resources. To measure the likelihood of these risks, we will use a scale of 1, meaning very unlikely, to 5, meaning very likely.

### 6.1. Hardware Risks

We made a list of a couple risks we will be facing in terms of hardware ordered from most likely to least likely but also with regard to importance:

- Complexity of circuitry
- Likelihood: 4
- Impact: 5
- Effect: Use of multiple electrical components with all associated risks that come with it. Will lead to burning/ruining components.
- Origin: Complexity will cause confusion on a hardware-level. This creates the risk
- Prevention: Keeping the circuitry as simple and modular as possible. Sanity checking the design with multiple people and staff before implementing.
- Insufficient power from motors (or hardware mismatch)
- Likelihood: 3
- Impact: 4
- Effect: Slower than expected mouse. One component can also become the weakest link, hindering other component capabilities (if motors are slow, then no use in getting top of the market gyros if our speed isn’t even fast enough)
- Origin: Miscalculation in design. Lack of foresight.
- Prevention: Go over the design and plan multiple times with different people. Make sure to think until the very end of the assembly process.
- Slippage on the new maze design
- Likelihood: 2
- Impact: 3
- Effect: Ratatoskr will not be able to make sharp turns. Slippage leads to uncertainty.
- Origin: Trying out a new design for the maze floor which differs from the previous year’s felted design.
- Prevention: We believe MDF provides sufficient friction for Ratatoskr’s tires. This belief, however, could be misplaced. In the worst-case scenario, we may use some rubberized coating seal, like Flex Seal or Plasti Dip.

### 6.2. Software Risks

There is also a list of software concerns we may likely face:

- I2C/Communication issues with hardware
- Likelihood: 5
- Impact: 3
- Effect: If software does not correctly communicate with hardware, we may face endless amounts of debugging and researching ways to bypass some restrictions left by I2C and our implementation.

- Origin: Lack of understanding or lack of infrastructure to seamlessly create an interface between the hardware we order and the software we make.
- Prevention: Ensure to have completely read through documentation on the components along with their interfaces, specifically how they connect to software. If a component seems to cause problems, we can either rethink the component choice or think of a workaround.
- Complexity of algorithms (algorithm mismatch)
- Likelihood: 3
- Impact: 2
- Effect: Nonoptimal attempts to solve/traverse the maze. Failed runs.
- Origin: Lack of understanding regarding the complexity of an algorithm or how it will be implemented. Perhaps choice of algorithm may not suit specific types of mazes, issues with scaling to bigger mazes.
- Prevention: We must keep an eye on the choice/complexity of the algorithm we will use for solving and traversing the maze in the shortest distance and fastest time. We should think of the different scenarios Ratatoskr may be put it (small mazes with an emphasis and speed or large mazes with an emphasis of time)

### 6.3. Human Resource Risks

Finally, we have a list of human-related issues and risk we will likely face.

- Bugs encountered when developing
- Likelihood: 4
- Impact: 3
- Effect: The scale and complexity of the project may cause issues for the developing team. Malfunctioning code could be detrimental to Ratatoskr in some cases like crashing into maze walls.
- Origin: Very likely but also very dependant on the team working on the project. It can be caused by either one person working on the code in its entirety and getting caught up by the complexity and scale, or it can due to lack of communication between the team members working on development. To add to this, debugging may be difficult with an autonomous piece of hardware. Live checks are not possible, thus hindering the debugging process.
- Prevention: Through modularly choosing sections and tasks for development, we can spread the work through multiple people who master their own implementation and can effectively communicate their code with others. Having multiple people on the code may also help with frequent sanity checks on code logic. Logging data when completing runs may also help tremendously with the debugging procedure.
- Mishandling of components
- Likelihood: 2
- Impact: 3
- Effect: May result in the destruction of the components we work with rendering them useless. That would in turn cause delays in the progress of the project (buying new components, figuring out fixes)
- Origin: Lack of experience regarding the components we are dealing with. Lack of super-vision when working with unfamiliar components.
- Prevention: Ensuring to check with more experienced people like the staff when it comes to unfamiliar hardware.

## 7. Bill of Materials

Links and prices as of 19.10.2025.

Part | Quantity | Price (CHF)
N20 DC Gear Motors 750RPM (https://www.digikey.ch/short/dnv38478) * | 2 | 31.92
MX1508 motor driver * | 1 | -
ESP32 development kit (30pin) (https://www.conrad.ch/fr/p/carte-de-developpement-joy-it-sbc-nodemcu-esp32-node-mcu-esp32-modul-1656367.html) | 1 | 10.95
LM2596 Stepdown Buck Converter (https://shopofthings.ch/sop/prototyping/power/lm2596-stepup-stepdown-buck-converter-variabel/) | 1 | 3.71
VL53L1X (TOF400C) ToF sensor (https://www.amazon.com/TOF400C-VL53L1X-Ranging-Flight-Distance/dp/B0DC6M6G7W?th=1) (set of 4) * | 1 | 16.66
MPU-6050 3-axis accelerometer with gyroscope (https://www.conrad.ch/de/p/joy-it-mpu6050-beschleunigungssensor-1-st-passend-fuer-entwicklungskits-bbc-micro-bit-arduino-raspberry-pi-rock-p-2136256.html) | 1 | 3.95
8x8 LED-Matrix w/ I2C Backpack (https://www.play-zone.ch/de/bauteile/led/segmente-matrix/dk-8x8-led-matrix-rot-mit-ht16k33-backpack.html) | 1 | 11.90
Adafruit MicroSD card breakout board (https://www.play-zone.ch/en/adafruit-microsd-card-breakout-board.html) | 1 | 12.90
18/27mm tires for RC cars (https://www.rc-shop.ch/reifen-felgen-676/rctiger-rc-fahrzeug-reifenfelgen-vorne-18-27mm-2-stueck-reifen-mini-z-128-30-sh-moosgummi-51359) (pair) | 2 | 5.00
9V battery + connector * | 1 | -
Total | - | 96.99

* components in stock for the course, as discussed
We need four tires total, as we might want to have four wheels on the mouse.

## 8. Inspiration and References

Last year’s micromice:
- MinosMouse: https://github.com/epfl-cs358/2024fa-minosmouse
- PicoMouse: https://github.com/epfl-cs358/2024fa-picomouse

Official micromouse rules: https://micromouseonline.com/micromouse-book/rules/

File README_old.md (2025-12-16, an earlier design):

# Ratatoskr

## Logistics

- Use `./src/` for source code (`.cpp`, `.c`) and for unit tests (`.test.cpp`).
- Use `./include/` for headers (`.hpp`, `.h`)
- Use `./tests/` for any other form of testing
- The `.clang-format` file specifies the formatting style and can be applied to all files using `make format`

### CAD

- Use `./CAD/STL` **only** for `.stl` files, preferably with a well-chosen name
- Use `./CAD/3D_print` **only** for `.3mf` files, preferably with a name related to the STL files it includes.

See below for an example.

#### Wheels

The final wheels `.stl` files are `./CAD/STL/rim_17.5x12.5mm_no_chamfer.stl` and `./CAD/STL/tire_17.5-27x12.5mm_treaded_0.75mm_tol.stl` which correspond to the wheel of width 12.5mm, tire inner diameter 17.5mm and tire outer diameter 27mm.  
The corresponding 3D printing files are:

- `./CAD/3D_print/rims_17.5x12.5mm_no_chamfer.3mf`
- `./CAD/3D_print/tires_17.5-27x12.5mm_treaded_0.75mm_tol.3mf` for the tires with -0.75mm diameter-tolerance

## PlatformIO usage

To compile the project run `pio run` from the command-line in the root directory.  
To upload the project run `pio run --target upload` from the command-line in the root directory.  
To open the serial monitor run `pio device monitor` from the command-line in the root directory.

> [!WARNING]
> Before doing anything for the first time, run `pio run --target compiledb` from the command-line in the root directory to generate `compile_commands.json` which tells `clangd` how to compile everything.

## Software

### Class Hierarchy

`gear_motor` - Class that controls the N20 Motor. Requires interrupt GPIO and PWM pins.
`gyro` - Class that handles interactions with the 6050 Gyroscope. Requires I2C pins.

`tof` - Class that handles interactions with the ToF Sensors. Requires I2C and GPIO pins.

`led_matrix` - [Deprecated] Class that controls the 8x8 LED Matrix.

`sd_card` - [Deprecated] Class that handles interactions with the SD Card.

`maze` - Class representation of the discovered part of the labyrinth. This class contains an array representation to track the walls as well as one for the distances to target. Further it maintains the targets and the visited coordinates.

`mouse` - Abstract class that outlines the interface a mouse (that can interact with the solver) should expose.

`ratatoskr`
`virtual_mouse`
`solver`

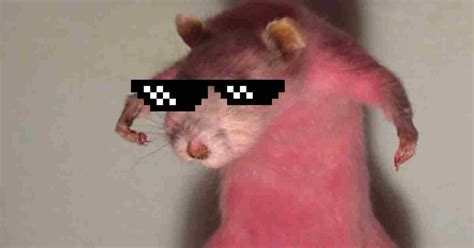
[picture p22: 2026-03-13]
proposal/img/rat2.png

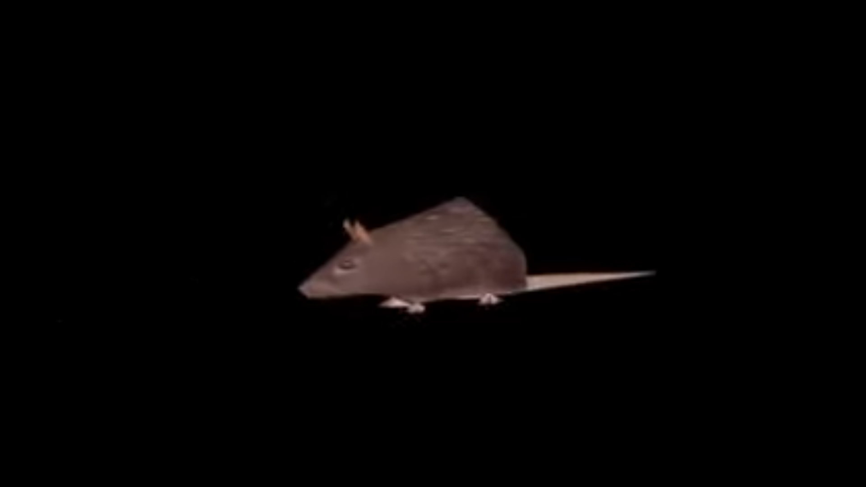
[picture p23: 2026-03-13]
proposal/img/rat.jpg

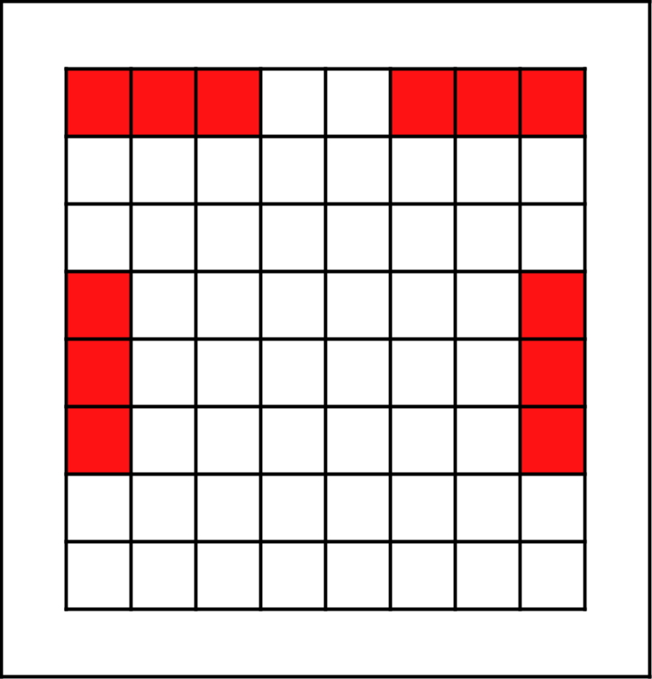
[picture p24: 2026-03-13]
proposal/img/ratatoskr_LED_matrix.png

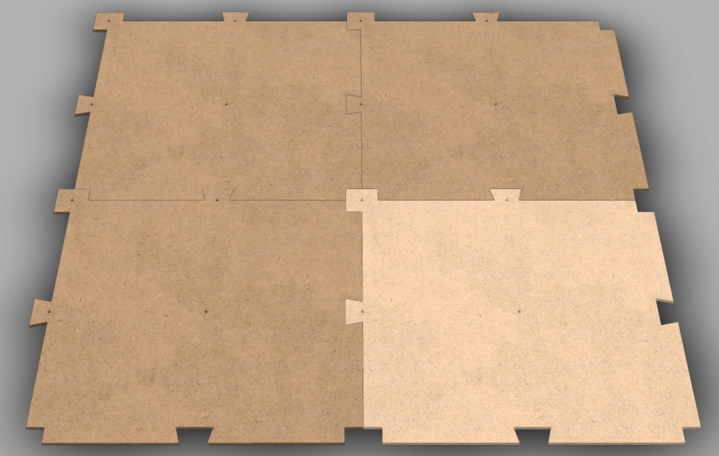
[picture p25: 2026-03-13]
proposal/img/MazeFloorTileCAD.png

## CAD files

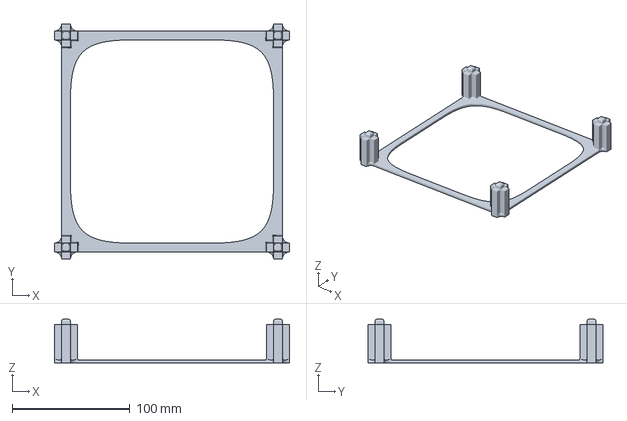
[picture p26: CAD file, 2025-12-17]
CAD/3D_print/cell_marker.3mf
199.6 x 199.6 x 37.3 mm

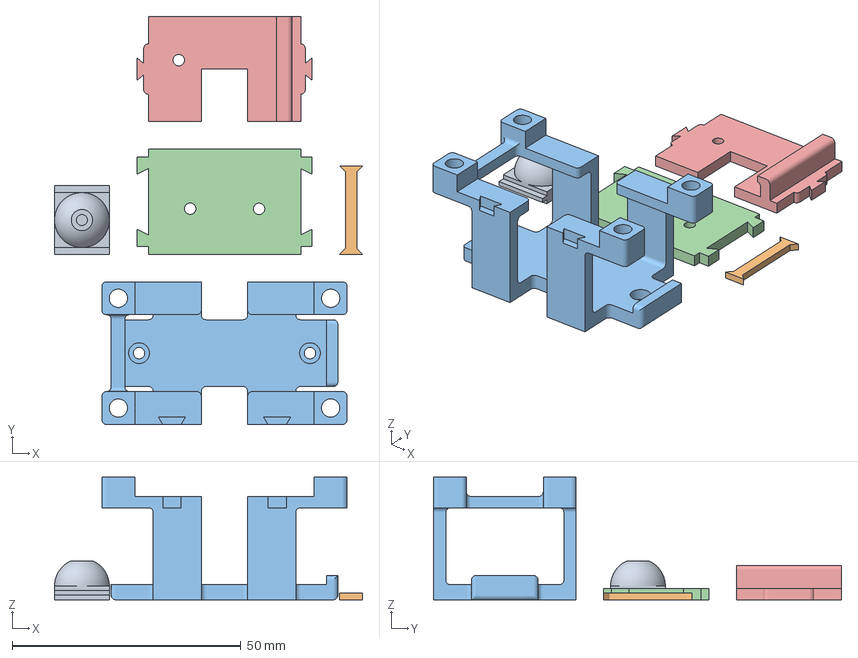
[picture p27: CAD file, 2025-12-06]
CAD/3D_print/v2/other_parts.3mf
67.3 x 89.2 x 26.8 mm
ball_caster.stl
battery_clip.stl
battery_holder.stl
middle_shelf.stl
top_shelf.stl

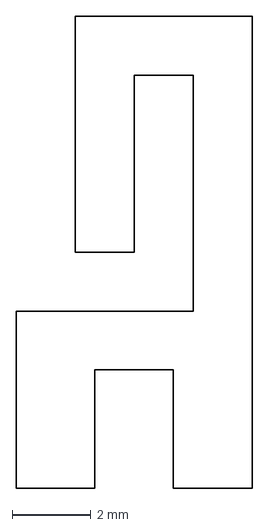
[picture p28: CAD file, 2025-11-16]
CAD/lasercut/cable_holder.dxf
6.00 x 12.0 mm

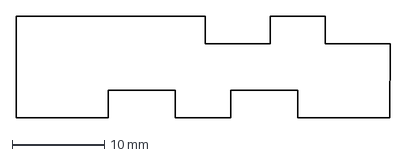
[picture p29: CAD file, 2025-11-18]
CAD/lasercut/calibration_cage/calibration_cage_lower_sidewall.dxf
40.5 x 11.0 mm

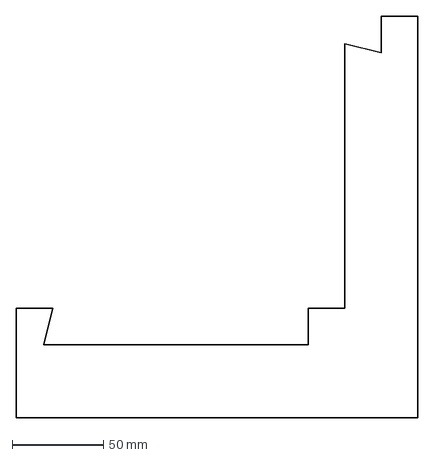
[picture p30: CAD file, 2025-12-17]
CAD/lasercut/maze/hybrid_corner_brace.dxf
220.0 x 220.0 mm

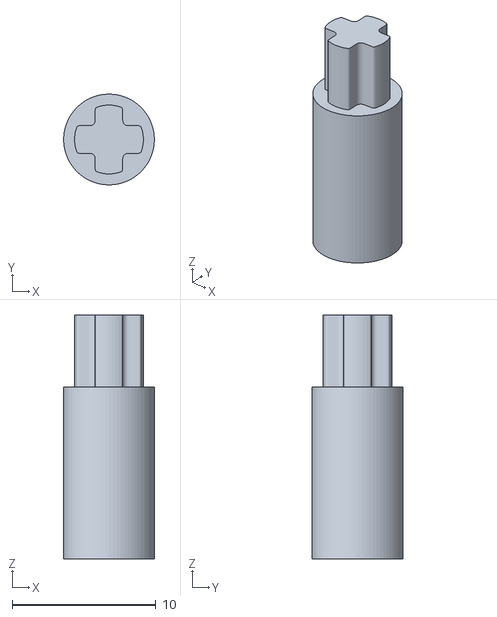
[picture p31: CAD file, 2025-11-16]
CAD/STL/lego_adapter_v2a.stl
6.32 x 6.32 x 17.0

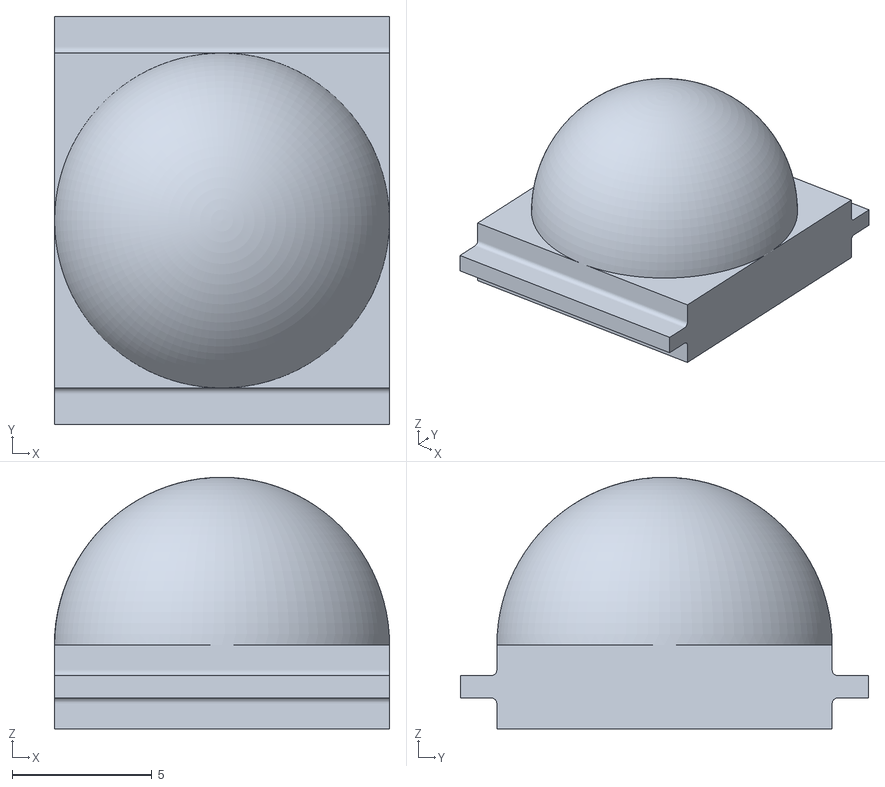
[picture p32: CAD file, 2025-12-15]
CAD/STL/v2/ball_caster.stl
12.0 x 14.6 x 9.00

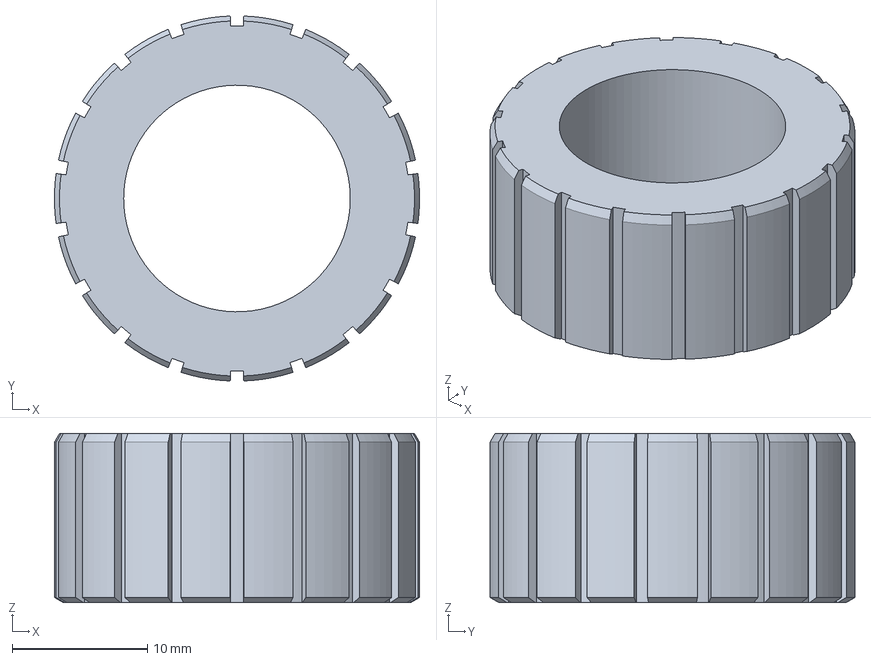
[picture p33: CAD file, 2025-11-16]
CAD/3D_print/tires_17.5-27x12.5mm_treaded_0.75mm_tol_fuzzy.3mf
27.0 x 27.0 x 12.5 mm

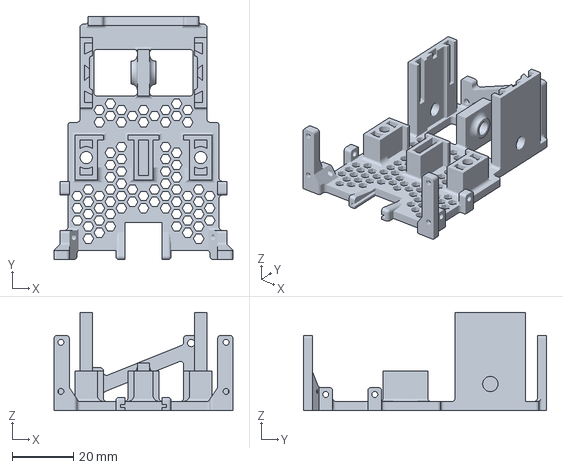
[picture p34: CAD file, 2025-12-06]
CAD/3D_print/v2/chassis.3mf
58.3 x 79.2 x 32.0 mm

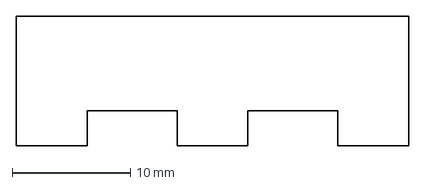
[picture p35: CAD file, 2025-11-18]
CAD/lasercut/calibration_cage/calibration_cage_upper_sidewall.dxf
33.2 x 11.0 mm

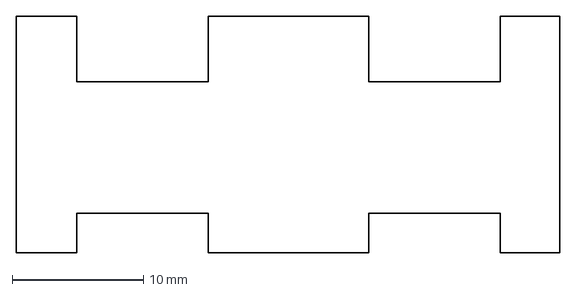
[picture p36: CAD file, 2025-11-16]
CAD/lasercut/jack_back_wall.dxf
41.3 x 18.0 mm

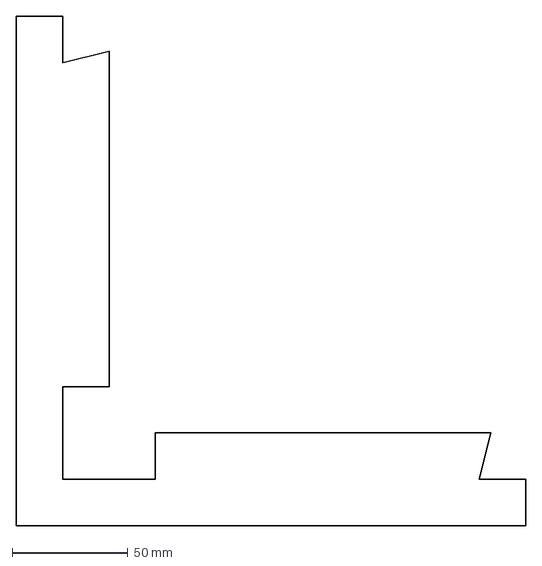
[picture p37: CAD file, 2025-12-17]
CAD/lasercut/maze/female_corner_brace.dxf
220.0 x 220.0 mm

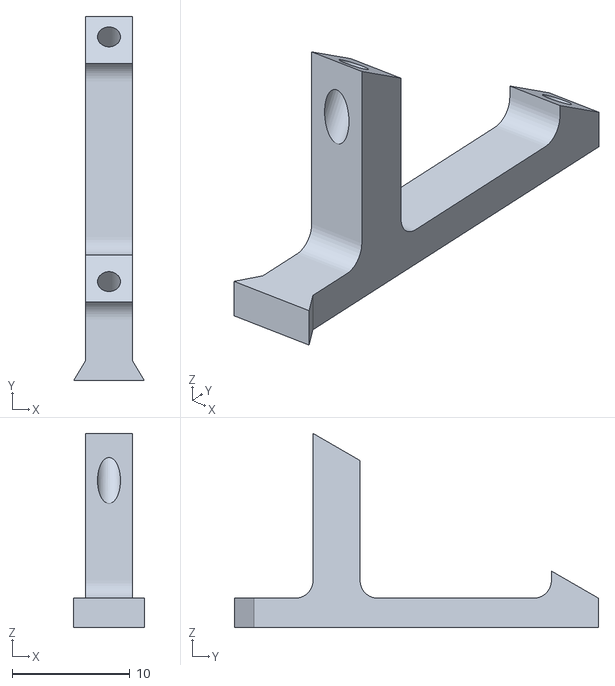
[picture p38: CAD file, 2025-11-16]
CAD/STL/screen_mount.stl
6.00 x 30.9 x 16.5

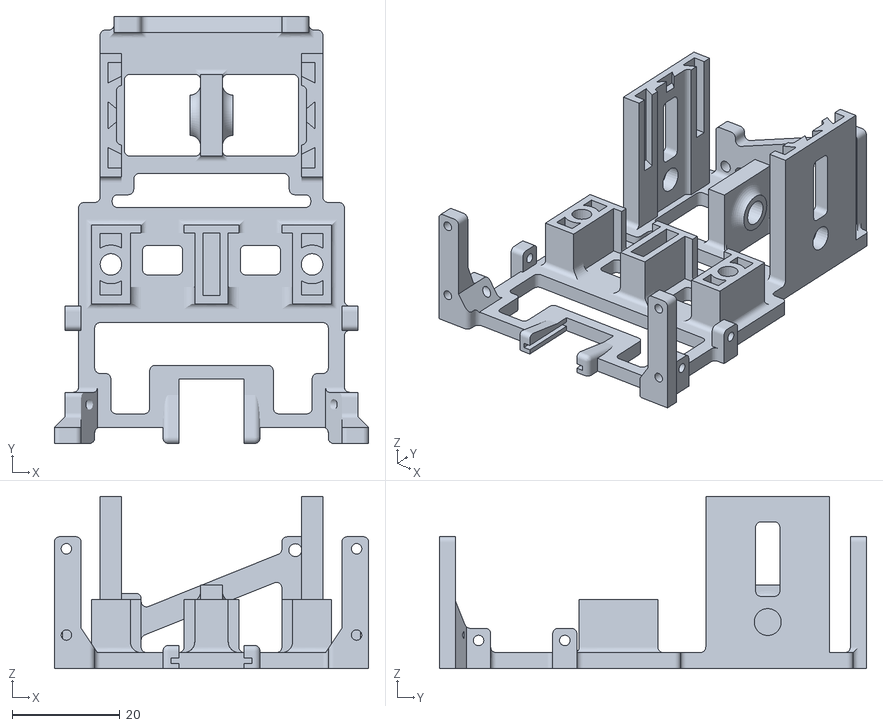
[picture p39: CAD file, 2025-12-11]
CAD/STL/v2/chassis_cutout.stl
58.3 x 79.2 x 32.0

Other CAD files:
CAD/3D_print/tires_17.5-27x12.5mm_treaded.3mf
CAD/lasercut/calibration_cage/calibration_cage_baseplate.dxf
CAD/lasercut/jack_front_wall.dxf
CAD/lasercut/maze/male_corner_brace.dxf
CAD/3D_print/rims_16x8mm.3mf
CAD/3D_print/rims_16x8mm_no_chamfer.3mf
CAD/3D_print/rims_17.5x12.5mm_no_chamfer.3mf
CAD/3D_print/tires_17.5-27x12.5mm_treaded_0.75mm_tol.3mf
CAD/3D_print/v1/body_parts.3mf
CAD/3D_print/v1/drive_train.3mf
CAD/3D_print/v1/ratatoskr_big_parts.3mf
CAD/3D_print/v1/ratatoskr_small_parts.3mf
CAD/STL/cell_marker.stl
CAD/STL/lego_adapter_v1.stl
CAD/STL/lego_adapter_v2b.stl
CAD/STL/miter_gear.stl
CAD/STL/rim_16x8mm.stl
CAD/STL/rim_16x8mm_no_chamfer.stl
CAD/STL/rim_17.5x12.5mm_no_chamfer.stl
CAD/STL/tire_17.5-27x12.5mm_treaded.stl
CAD/STL/tire_17.5-27x12.5mm_treaded_0.75mm_tol.stl
CAD/STL/v1/axle_holder.stl
CAD/STL/v1/battery_holder.stl
CAD/STL/v1/buck_holder.stl
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

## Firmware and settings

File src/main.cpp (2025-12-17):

#include <Arduino.h>

#include "config.hpp"
#include "esp_logger.hpp"
#include "oled.hpp"
#include "pins.hpp"
#include "ratatoskr.hpp"
#include "solver.hpp"
#include "util.hpp"

using namespace Config;

/* TODO: Right now you have to change this by hand. */
const MODE mode = RUN;

ToF tof_left = ToF(LEFT, TOF_LEFT_ADDRESS, TOF_LEFT_XSHUT);
ToF tof_front_left =
    ToF(FRONT_LEFT, TOF_FRONT_LEFT_ADDRESS, TOF_FRONT_LEFT_XSHUT);
ToF tof_front_right =
    ToF(FRONT_RIGHT, TOF_FRONT_RIGHT_ADDRESS, TOF_FRONT_RIGHT_XSHUT);
ToF tof_right = ToF(RIGHT, TOF_RIGHT_ADDRESS, TOF_RIGHT_XSHUT);

MPU6050 gyro = MPU6050();

OLED oled = OLED();

/* encoder_sign (default = 1) determines the direction */
GearMotor motor_left(MOTOR_L_IN1, MOTOR_L_IN2, 0, 1, /* PWM channels */
                     ENC_L_OUT1, ENC_L_OUT2, 255,    /* max PWM */
                     +1 /* encoder_sign (I tested) */
);

GearMotor motor_right(MOTOR_R_IN1, MOTOR_R_IN2, 2, 3, /* PWM channels */
                      ENC_R_OUT1, ENC_R_OUT2, 255,    /* max PWM */
                      -1 /* encoder_sign (I tested) */
);

Maze maze;
Ratatoskr rat(motor_left, motor_right, tof_left, tof_front_left,
              tof_front_right, tof_right, gyro, oled);
Solver solver(rat, maze);

void setup() {
    /* ToF XSHUT pins */
    pinMode(TOF_LEFT_XSHUT, OUTPUT);
    pinMode(TOF_FRONT_LEFT_XSHUT, OUTPUT);
    pinMode(TOF_RIGHT_XSHUT, OUTPUT);
    pinMode(TOF_FRONT_RIGHT_XSHUT, OUTPUT);

    Wire.begin();
    delay(500);
    Serial.begin(115200);
    delay(500);
    gyro.begin();
    delay(500);
    oled.begin();
    delay(500);

    tof_left.begin();
    tof_front_left.begin();
    tof_right.begin();
    tof_front_right.begin();

    /* ---- ENCODER INTERRUPT SETUP (integrated with GearMotor) ---- */
    /* Use ESP32's attachInterruptArg so each motor instance gets its
     * own ISR arg */
    attachInterruptArg(ENC_L_OUT1, GearMotor::isr_trampoline, &motor_left,
                       RISING);

    attachInterruptArg(ENC_R_OUT1, GearMotor::isr_trampoline, &motor_right,
                       RISING);

#ifdef CALIBRATE
    tof_left.calibrate_sensor(TOF_SIDE_EXPECTED_MM);
    tof_front_left.calibrate_sensor(TOF_FRONT_EXPECTED_MM);
    tof_front_right.calibrate_sensor(TOF_FRONT_EXPECTED_MM);
    tof_right.calibrate_sensor(TOF_SIDE_EXPECTED_MM);
#endif

    switch (mode) {
        case DEBUG: {
            oled.mode = DEBUG;
            logger_enabled = true;
            /* WARN: no break on purpose cause we want to fall through to RUN */
        }

        case RUN: {
            std::vector<Instruction>* instr = new std::vector<Instruction>;
            if (!ESPLogger::retrieve_solution(*instr)) {
                /* push target to maze */
                maze.set_targets(END_POINTS);

                solver.solve(); /* run from start to target */

                /* push start to maze */
                maze.set_targets(START_POINTS);
                solver.solve(); /* run from target to start */

                maze.set_targets(END_POINTS);
                solver.finalize_discovery();
                std::vector<GraphCoordinate>* solved =
                    new std::vector<GraphCoordinate>;
                solver.dijkstra(*solved, true);
                solver.parse_path(*solved, *instr);
                delete solved;
                ESPLogger::write_solution(*instr);
            }
            solver.run(*instr);
            ESPLogger::clear_sol();
            delete instr;
            ESPLogger::clear_logs();

            rat.update_screen(0.0f, HAPPY);
            /* TODO: dance (jiggy) */

            break;
        }

        case DUMP_LOG: {
            logger_enabled = true;
            ESPLogger::export_logs();
            ESPLogger::clear_logs();
            break;
        }

        case TESTING: {
            oled.mode = DEBUG;
            rat.moveDiagonal(2.0);
            rat.turnLeft();
            rat.moveDiagonal(0.5);
            rat.turnLeft45();
        }
    }
}

/* WARNING: DO NOT USE THIS, WEIRD BEHAVIOR WITH LEDC AND PINS!!!!! */
void loop() {}

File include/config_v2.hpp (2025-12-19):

#pragma once

#include <cstdint>
#include <vector>

#include "util.hpp"

namespace Config {
/* ========================================================================== */
/* |                                  maze                                  | */
/* ========================================================================== */
constexpr int MAZE_WIDTH = 9;
constexpr int MAZE_HEIGHT = 9;

const std::vector<Position> START_POINTS = {Position(0, 0)};
const std::vector<Position> END_POINTS = {Position(6, 6)};

constexpr int CELL_SIZE_MM = 180;
constexpr int WALL_TO_WALL_MM = 160;

/* ========================================================================== */
/* |                                movement                                | */
/* ========================================================================== */
constexpr int TURN_PWM = 187;
constexpr int TURN_TIME_LIMIT = 2000;
constexpr float TURN_TRESHOLD = 3.f;

constexpr uint8_t FORWARD_PWM = 181;
constexpr uint8_t FORWARD_FAST_PWM_CHUNK = 25;
constexpr uint8_t FORWARD_FAST_PWM_MAX = 200;
constexpr float FORWARD_OVERSHOOT_SLOPE = 0.02f;
constexpr int STOP_DISTANCE = 55;
/* ========================================================================== */
/* |                               dimensions                               | */
/* ========================================================================== */
constexpr uint8_t WIDTH_MM = 70;
constexpr float DIST_BETWEEN_SENSORS_MM = 53.75f;

/* ========================================================================== */
/* |                               motor stuff                              | */
/* ========================================================================== */
constexpr uint8_t GEARING = 30;
constexpr uint8_t ENCODER_MULTIPLIER = 6;

/* measured by pushing the mouse exactly one cell length */
constexpr uint16_t ENCODER_COUNTS_PER_CELL = 250;

/*  encoder counts per mm = counts per cell / cell size */
constexpr float ENCODER_COUNTS_PER_MM =
    static_cast<float>(ENCODER_COUNTS_PER_CELL) /
    static_cast<float>(CELL_SIZE_MM);

constexpr float PWM_UPDATE_RATIO = .6f;
constexpr float MAX_PWM_CORRECTION = 30.0f;

/* ========================================================================== */
/* |                                ToF stuff                               | */
/* ========================================================================== */
constexpr uint8_t TOF_LEFT_ADDRESS = 0x30;
constexpr uint8_t TOF_FRONT_LEFT_ADDRESS = 0x31;
constexpr uint8_t TOF_FRONT_RIGHT_ADDRESS = 0x32;
constexpr uint8_t TOF_RIGHT_ADDRESS = 0x33;

/*  beyond this: treat as "no wall" */
constexpr uint16_t MAX_TOF_VALID_MM = 120;
/*  front considered blocked if any front ToF < this */
constexpr uint16_t FRONT_WALL_MM = 110;
/*  side considered blocked if side ToF < this */
constexpr uint16_t SIDE_WALL_MM = 90;

constexpr uint16_t TOF_SIDE_EXPECTED_MM = 50;      /* ----------------- */
constexpr uint16_t TOF_FRONT_EXPECTED_MM = 40;     /* | measured and  | */
constexpr int16_t TOF_LEFT_OFFSET_MM = -36;        /* | calibrated in | */
constexpr int16_t TOF_FRONT_LEFT_OFFSET_MM = -19;  /* | calibration   | */
constexpr int16_t TOF_FRONT_RIGHT_OFFSET_MM = -1;  /* | cage (TM)     | */
constexpr int16_t TOF_RIGHT_OFFSET_MM = -1;        /* ----------------- */

/* ========================================================================== */
/* |                                diagonals                               | */
/* ========================================================================== */
const float MAX_DIST_MM = 200.0f;
}  // namespace Config

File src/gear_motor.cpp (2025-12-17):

#include "gear_motor.hpp"

#include "config.hpp"

using namespace Config;

void IRAM_ATTR GearMotor::isr_trampoline(void *obj) {
    ((GearMotor *)obj)->encoder_interrupt();
}

GearMotor::GearMotor(int in1, int in2, int ch1, int ch2, int encoder_pin_1,
                     int encoder_pin_2, int max_pwm, int encoder_sign)
    : IN1(in1),
      IN2(in2),
      CH1(ch1),
      CH2(ch2),
      ENCODER_PIN_1(encoder_pin_1),
      ENCODER_PIN_2(encoder_pin_2),
      m_encoder_count(0),
      m_delta_time(0),
      m_t_last_i(0),
      m_max_pwm(max_pwm),
      m_encoder_sign(encoder_sign) {
    // Motor pins and PWM setup
    pinMode(IN1, OUTPUT);
    pinMode(IN2, OUTPUT);

    ledcSetup(CH1, MOTOR_FREQ, MOTOR_RES);
    ledcSetup(CH2, MOTOR_FREQ, MOTOR_RES);
    ledcAttachPin(IN1, CH1);
    ledcAttachPin(IN2, CH2);

    // Start stopped
    ledcWrite(CH1, 0);
    ledcWrite(CH2, 0);

    // Encoder pins (quadrature A/B) – interrupt will be attached on A
    pinMode(ENCODER_PIN_1, INPUT);
    pinMode(ENCODER_PIN_2, INPUT);
}

void IRAM_ATTR GearMotor::encoder_interrupt() {
    uint32_t t_curr_i = micros();
    if (m_t_last_i < t_curr_i) {
        m_delta_time = t_curr_i - m_t_last_i;
    }
    m_t_last_i = t_curr_i;

    // Quadrature direction logic
    int a = digitalRead(ENCODER_PIN_1);
    int b = digitalRead(ENCODER_PIN_2);

    // On a rising edge of A, A should be HIGH; direction depends on B.
    // The sign convention can be flipped with m_encoder_sign so that
    // one GearMotor can behave like left and another like right.
    if (a > b) {
        m_encoder_count -= m_encoder_sign;
    } else {
        m_encoder_count += m_encoder_sign;
    }
}

int GearMotor::get_rpm() {
    /* avoid division by zero */
    if (m_delta_time == 0) {
        return 0;
    }

    float revolutions = static_cast<float>(m_delta_time); /* µs */
    revolutions = 1.0f / revolutions;                     /* rev per µs */
    revolutions *= 1000000.0f;                            /* rev per sec */
    revolutions *= 60.0f;                                 /* rev per min */
    revolutions /= GEARING;            /* account for gear ratio */
    revolutions /= ENCODER_MULTIPLIER; /* ticks per rotation */

    return static_cast<int>(revolutions);
}

void GearMotor::setSpeed(int speed) {
    speed = constrain(speed, -m_max_pwm, m_max_pwm);

    if (speed >= 0) {
        ledcWrite(CH1, speed);
        ledcWrite(CH2, 0);
    } else {
        ledcWrite(CH1, 0);
        ledcWrite(CH2, -speed);
    }
}

void GearMotor::spin_cw(int speed) { setSpeed(abs(speed)); }

void GearMotor::spin_ccw(int speed) { setSpeed(-abs(speed)); }

void GearMotor::coast() { setSpeed(0); }

void GearMotor::brake() {
    ledcWrite(CH1, m_max_pwm);
    ledcWrite(CH2, m_max_pwm);
}

long GearMotor::get_encoder_count() { return m_encoder_count; }

void GearMotor::reset_encoder_count() { m_encoder_count = 0; }

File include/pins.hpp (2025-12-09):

#pragma once
#include <cstdint>
// ToF
constexpr uint8_t TOF_LEFT_XSHUT = 15;
constexpr uint8_t TOF_FRONT_LEFT_XSHUT = 18;
constexpr uint8_t TOF_FRONT_RIGHT_XSHUT = 19;
constexpr uint8_t TOF_RIGHT_XSHUT = 23;

// I2C
#if (defined SDA && defined SCL)
constexpr uint8_t SDA = 0x21;
constexpr uint8_t SCL = 0x22;
#endif

// Motor / Encoder

/* left motor, pins in order of ESP => motor A resp. 1 */
constexpr uint8_t MOTOR_L_IN1 = 12;
constexpr uint8_t MOTOR_L_IN2 = 14;
constexpr uint8_t ENC_L_OUT1 = 33;
constexpr uint8_t ENC_L_OUT2 = 32;

/* right motor, pins in order of ESP => motor B resp. 2 */
constexpr uint8_t MOTOR_R_IN1 = 27;
constexpr uint8_t MOTOR_R_IN2 = 26;
constexpr uint8_t ENC_R_OUT1 = 35;
constexpr uint8_t ENC_R_OUT2 = 34;

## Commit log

2025-10-19 [#4] Update project proposal (BoM)
    Fix quantity of motor driver board (1 -> 2) as the new board we are
    using only supports one motor, not two.
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2025-10-28 Header file for the motor class (#19)
    - Method and attribute headers according to the proposal (p. 5)
    - Depending on implementation these things might change.
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2025-10-29 [#17] Update libraries and restructure approach
    Better libraries are being used for the interface.
    ToF sensors now inherit from one parent class.
    Each individual subclass uses the corresponding API calls
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2025-10-30 [#17] Remove String and replace with enum
    We also remove overhead caused my m_initialized as it seems redundant.
    If it is set true in constructor, and not changed anywhere else, the
    check to see if it is initialized is to simply see if the object exists.
    [ToF.cpp]
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2025-10-31 Fixed uint16_t casting in readRaw and other minor bugs
    [gyro.cpp]
2025-11-03 [#20] Add first (very basic) implementation of hardware for LED matrix
    current features:
    - draw and clear walls
    - clear entire matrix
2025-11-03 [#20] Rename led.[ch]pp to led_matrix.[ch]pp cause frankly, what was I thinking
    led_matrix is a much more descriptive name
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2025-11-03 Simplify GearMotor class, fix rpm code [#19]
    also rename files
    [gear_motor.cpp]
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2025-11-04 [#35] Add STL, 3MF and gcode of the rims for the 16x8mm (inner x width) tires
    3D design is on Fusion360
    [rim_16x8mm.stl, rims_16x8mm.3mf]
2025-11-04 [#35] Update rims
    [rims_16x8mm.3mf]
2025-11-04 [#35] Add new version of rims without chamfers as they mess up the 3D printing
    Also, I used the wrong filament settings whoopsies
    [rim_16x8mm_no_chamfer.stl, rims_16x8mm.3mf, rims_16x8mm_no_chamfer.3mf]
2025-11-04 [#35] Add new new rims based on the LEGO wheel (3MF and STL)
    [rim_17.5x12.5mm_no_chamfer.stl, rims_17.5x12.5mm_no_chamfer.3mf]
2025-11-05 [#17] Fixing the constructor of TOF class.
    - did not use irq and shutdown necessary to initialize the library
    [ToF.cpp]
2025-11-06 Fixed switch case bug in gyro.cpp
    [gyro.cpp, gyro.hpp]
2025-11-06 [#41] Add STL, 3MF and gcode of the treaded tires for the 17.5x12.5 rims
    The rims have also been updated
    [rims_17.5x12.5mm_no_chamfer.3mf, tire_17.5-27x12.5mm_treaded.stl, tires_17.5-27x12.5mm_treaded.3mf]
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2025-11-07 [#41] Add new version of treaded tire with smaller inner diameter for better fit
    [tire_17.5-27x12.5mm_treaded_0.75mm_tol.stl, tires_17.5-27x12.5mm_treaded_0.75mm_tol.3mf]
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2025-11-07 [#19] Forgot iram attr and fixed superfluous ;
    [gear_motor.cpp]
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2025-11-07 Changed swtich case to map and fixed include
    [gyro.cpp]
2025-11-07 [#25] Add .dxf and LightBurn files for lasercutting the MDF parts
    [baseplate.dxf, drivetrain_housing_middle_shelf.dxf, drivetrain_housing_sidewall.dxf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]
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2025-11-07 [#25] Add STL and 3MF files
    [body_parts.3mf, buck_holder.stl, drive_train.3mf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]
2025-11-07 [#25] Add axle_holder and update drive_train
    [axle_holder.stl, drive_train.3mf]
2025-11-07 [#25] Update baseplate.dxf as some parts were way too thin leading to breaks
    [baseplate.dxf]
2025-11-07 [#25] Add more time-efficient 3mf files
    [ratatoskr_big_parts.3mf, ratatoskr_small_parts.3mf]
2025-11-07 [#25] move 3mf files, add v2 of sensor bracket & baseplate, update gyro mounts
    [baseplate_v1.dxf, baseplate_v2.dxf, body_parts.3mf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]
2025-11-08 [#25] Update .3mf files to include new versions
    [motor_bracket_v1.stl, motor_bracket_v2.stl, ratatoskr_big_parts.3mf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]
2025-11-08 [#25] Fix .dxf files to not have overlapping lines, update Lightburn file
    [drivetrain_housing_middle_shelf.dxf, drivetrain_housing_sidewall.dxf, drivetrain_housing_top_shelf.dxf]
2025-11-09 [#25] Update .dxf files for sidewall and middle shelf, update LightBurn file
    Reduce hole distance in middle shelf for axle holder
    Reduce axle through hole diameter
    [drivetrain_housing_middle_shelf.dxf, drivetrain_housing_sidewall.dxf]
2025-11-09 [#25] Add tolerance to gear and wall in axel holder
    [axle_holder.stl, miter_gear.stl]
2025-11-09 [#25] Add v3 of motor bracket which adds nut holes and threaded insert holes
    also update .3mf of big parts
    [motor_bracket_v3.stl, ratatoskr_big_parts.3mf]
2025-11-09 [#25] Fix buck_holder as the hole distance and size was wrong
    [buck_holder.stl, ratatoskr_small_parts.3mf]
2025-11-10 Fix some bugs with library includes and ratatoskr
    -Arduino include causing problems with MMS\
    -Ali's code not having types and semi colons (python lol)
    -Added comment about logging in virtual_mouse.cpp
    [ratatoskr.cpp]
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2025-11-10 [#25] Add .dxf files for jack thingy
    [jack_back_wall.dxf, jack_baseplate.dxf, jack_front_wall.dxf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]
2025-11-10 [#36] Fixes constructor of ratatoskr class and adds clarifying comments
    [ratatoskr.cpp]
2025-11-10 [#24] Add TODOs and fix constructor of Ratatoskr
    [ratatoskr.cpp]
2025-11-10 [#25] Add battery_holder and update small_parts
    [battery_holder.stl, ratatoskr_small_parts.3mf]
2025-11-11 [#25] Add v2 of lego_adapter to fix the wobblyness of the driven gear
    sholeh looking adapter
    [lego_adapter_v1.stl, lego_adapter_v2.stl]
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2025-11-13 [#54] Fix small type issue
    [ToF.cpp]
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2025-11-14 [#25] Add v2.5 of lego_adapter with smaller shaft diameter, add cable_holder
    [cable_holder.dxf, cable_holder_support.dxf, lego_adapter_v2a.stl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]
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2025-11-16 Fixed getAngle and added bias in reading gyro
    [gyro.cpp]
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2025-11-16 [#47] Add ToF interface solved in #54
    [ToF.cpp]
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2025-11-16 [#47] Fix imports of ToF.hpp as Windows is dumb and paths aren't case-sensitive
    [ToF.cpp]
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2025-11-16 Make main compile again, fix pin definitions in pins.hpp
    [ToF.cpp, main.cpp, pins.hpp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]
2025-11-16 [#47] Fix gyro calibration issue
    [gyro.cpp, main.cpp, ratatoskr.cpp]
2025-11-16 [#63] fixes + now with clear funciton
    [logger.cpp, main.cpp]
2025-11-16 [#56] Add .3mf file for fuzzy skin tires which are very nice and grippy
    [tires_17.5-27x12.5mm_treaded_0.75mm_tol_fuzzy.3mf]
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2025-11-17 Fix main branch by removing erroneous '{' in ToF.cpp and redefinition of PI
    [ToF.cpp]
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2025-11-18 [#81] Add .dxf files for calibration cage and LightBurn file
    [calibration_cage_baseplate.dxf, calibration_cage_holder.dxf, calibration_cage_lower_sidewall.dxf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]
2025-11-18 [#81] Add test file for calibration of all sensors. Make begin to construct correctly.
    Start was not good and if we wish to construct objects out of scope,
    init won't happen. So replicate what other classes do (gyro) and make
    begin the initializer
    [ToF.cpp, calibrate.cpp]
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2025-11-19 [#75] Fixing the pid :)
    [main.cpp, ratatoskr.cpp]
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2025-11-20 [#89] Fix naming convention and dumb function names
    [gear_motor.cpp]
2025-11-20 [#89] Fix dumb requirement for int16
    [gear_motor.cpp]
2025-11-21 [#89] Avoiding time loss in tof
    [ToF.cpp]
2025-11-21 [#94] Small function that stops moveForward in ratatoskr such that we dont crash
    [main.cpp, ratatoskr.cpp]
2025-11-22 [#79] New assumptions and ad-hoc solution for run finding
    There are some tricky mazes where the current Implementation of the
    shortest path does not work, so I created a simple alternative
    bfs_shortest_path that will find the shortest path without edge weights.
    The crucial insight that made this simplification possible was the fact
    that during the speedy run we should no longer make any assumptions that
    could shoot us in the foot. I created a method finalize_discovery to
    label any wall position we did not gain any information on during the
    discovery runs as containing a wall.
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2025-11-26 Fix erroneous fabsf() call
    [gyro.cpp]
2025-11-26 [#87] Keeping the PID up to date with the implementation
    - time_step is now a parameter and no longer a field
    - removes the bounds
    - removes unnecessary parameters from the constructor
    [ratatoskr.cpp]
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2025-11-26 [#87] Fix bug in turn(), parameters not yet correctly adjusted
    The bug was caused that no BASE_PWM was used
    [main.cpp, ratatoskr.cpp]
2025-11-26 [#87] this may be my worst commit, but the results are worth it (fix turning from 0 to 180)
    [ratatoskr.cpp]
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2025-11-28 [#30] Add maze .dxf files including braces and LightBurn file
    [female_brace.dxf, male_brace.dxf, tile_v2_4x4.dxf]
2025-12-01 [#101] Filter out 2x 45 deg turns and replace with 90 deg turn
2025-12-01 [#95] Add error correction to turning
    [ratatoskr.cpp]
2025-12-01 [#95] Fix for negative angles
    [ratatoskr.cpp]
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2025-12-01 [#95] Only reset PID when rotating
    [main.cpp, ratatoskr.cpp]
2025-12-01 Add snapToAngle to correct offset of mouse
    [ratatoskr.cpp]
2025-12-01 [#95] Gyro for slow turns didnt work, fix it
    [gyro.cpp]
2025-12-01 [#95] Fix issue where mouse divebombs left when no wall
    [ratatoskr.cpp]
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2025-12-01 [#95] Fix condition to hold on to one wall
    [main.cpp, ratatoskr.cpp]
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2025-12-02 [#38] Remove obsolete last_millis attribute member of OLED, use correct getAngle
    [oled.hpp, ratatoskr.cpp]
2025-12-06 [#51] Move all v1 files to separate folder
    [axle_holder.stl, battery_holder.stl, body_parts.3mf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]
2025-12-06 [#51] Add v2 .stl files
    [ball_caster.stl, battery_clip.stl, battery_holder.stl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]
2025-12-06 [#51] Add v2 .3mf files
    [chassis.3mf, other_parts.3mf]
2025-12-06 [#51] Update chassis.3mf to be printed on the MK4 cause he go brr
    [chassis.3mf]
2025-12-06 [#51] Fix chassis to hopefully be more rigid
    [chassis.stl, middle_shelf.stl]
2025-12-06 [#51] Add honeycomb variants of top_shelf, middle_shelf, chassis
    [chassis_honeycomb.stl, middle_shelf_honeycomb.stl, top_shelf_honeycomb.stl]
2025-12-06 [#51] Update .3mf files with honeycomb parts
    [chassis.3mf, other_parts.3mf]
2025-12-06 [#51] Add calibration cage adapter for new version
    [calibration_cage_adapter.stl]
2025-12-06 [#118] Rework config, add v2 config with minor changes
    [ToF.cpp, config_v1.hpp, config_v2.hpp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]
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2025-12-08 [#123] Add check to ToF::get_reading to only return the value if it's reasonable
    also fix all uses of ToF::read to ToF::get_reading
    [ToF.cpp, ratatoskr.cpp]
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2025-12-08 [#110] Fix casting for moveForward
    [ratatoskr.cpp]
2025-12-08 [#110] fixing merge problems
    [ratatoskr.cpp]
2025-12-09 [#110] Fix simulator issues
    [config_v1.hpp, config_v2.hpp]
2025-12-09 [#110] Fix formatting in config files
    [config_v1.hpp, config_v2.hpp]
2025-12-09 [#110] Re-add failsafe, clean up code a bit
    [ratatoskr.cpp]
2025-12-09 [#110] Fix moveForwardHalf signature so that it's actually called
    [ratatoskr.cpp]
2025-12-09 [#134] Fix bug and remove solution from tail if success
    [esp_logger.cpp, main.cpp]
2025-12-10 Add new version of chassis with cutouts instead of honeycomb
    [chassis_cutout.stl]
2025-12-15 Add new ball caster STL without screw hole
    [ball_caster_no_hole.stl]
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2025-12-16 [#131] Fix turning and speed only 80%
    [config_v2.hpp, ratatoskr.cpp]
2025-12-16 [#131] Fix call to deprecated function after rebase
    [ratatoskr.cpp]
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2025-12-16 [#131] Welcome back moveStraightMM, we missed you (use that for half)
    [ratatoskr.cpp]
2025-12-16 [#131] Find problem accumulator
    [ratatoskr.cpp]
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2025-12-16 [#131] Adjust config for swapped out ToFs
    [config_v2.hpp]
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2025-12-16 [#131] Max Jitter and also blank for left turn
    [ratatoskr.cpp]
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2025-12-16 [#145] Add cell marker stl and 3mf
    [cell_marker.3mf, cell_marker.stl]
2025-12-16 [#146] Add corner brace .dxf and .lbrn2 files
    [female_corner_brace.dxf, hybrid_corner_brace.dxf, male_corner_brace.dxf]
2025-12-16 [#145] Update cell marker files as the first iteration sucked
    [cell_marker.3mf, cell_marker.stl]
2025-12-17 [#149] Rename ball caster STLs to be more descriptive
    [ball_caster.stl, ball_caster_no_hole.stl, ball_caster_screw.stl]
2025-12-17 [#131] Moving the if branches into the while loop in moveForwardHalf jitter case
    [ratatoskr.cpp]
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
